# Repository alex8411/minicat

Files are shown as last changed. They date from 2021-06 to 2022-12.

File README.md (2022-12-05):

# minicat
## What's it minicat?
MiniCat is an open source (MIT licence) DIY Robot for Makers and Kids based on Arduino Nano :

- original design (3D parts, hardware, software): [open cat](https://github.com/petoicamp/opencat)
  from: [Rongzhong Li](https://www.linkedin.com/in/rongzhongli/) 

- first training material 
  created by [Lilie Boizumault](https://www.linkedin.com/in/lilie-boizumault/)

- starting from a first prototype below: 

SAM_5404_idle

I developed a plug and play variant of the robot to make it easier to build and understand :

PCB_MiniCat_with_1xServoMG90S_and_2x18650Batteries

MiniCat Robot - Robotics for Makers__MAIN

## Goals

Build a robot with kids and adults that is open source and affordable,
take a look on a comparaison of other kits made by ["le monde"](https://www.lemonde.fr/guides-d-achat/article/2020/06/13/les-meilleurs-kits-robots-pour-les-debutants_6042730_5306571.html)

All the workshops slides are available here under the /Workshop folder

## How pull request

1. Fork the project
2. `$ git clone https://github.com/<your-username>/minicat`
3. `$ cd minicat`
4. `$ git checkout -b branch-name`
5. edit, commit, push file
6. on your browser, in your repo, a button appear (compare and pull request), clic on

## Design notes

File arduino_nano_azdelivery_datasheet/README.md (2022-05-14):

Please find :

- the AzDelivery Arduino Nano clone datasheet : to check all pins available on the board

- the Arduino Nano board official schematics from :
https://www.arduino.cc/en/uploads/Main/Arduino_Nano-Rev3.2-SCH.pdf

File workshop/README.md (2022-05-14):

those are the slides used for MiniCat Robotics/Arduino workshops at Schools, Fablabs/Makerspaces, public events :

- Robotics_for_Makers_MiniCat_Assembly_Guide.pdf : if you want to print and assemble your whole robot !
- Robotics for Makers_Workshop_and_Curriculum.pdf : if you want to get a touch on designing/printing parts, assemble the electronics and program it!

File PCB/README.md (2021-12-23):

MiniCat_2.0_PCB_1_0.fzz is the 2 layers PCB (Printed Circuit Board, top and bottom) for the MiniCat 2.0 robot.

A PCB basically spares you all the manual wires connections that were done in MiniCat 1.0.

This avoids manual connections errors and add robustness to the prototype.
In that way you can concentrate on the different processing, actuators and sensors.

It allows a highly modular / easy to assemble robot.

You can connect all the modules step by step and test them with the related Arduino Software :
- Module 1 : Arduino main Microcontroller board
- Module 2 : Buzzer
- Module 3 : Infrared Receiver
- Module 4 : I2C bus connection between main Arduino Microcontroller board and MPU (Gyroscope)
- Module 5 : MPU (Gyroscope)
- Module 6 : Servo Motors and Driver board (tested together with MiniCat final Software)

MiniCat_2.0_PCB_1x_LAYER_1_0.fzz implements the same connections but this time on 1 top layer only.
This was optimized in order to be able to prototype the PCB on a CNC Mill.

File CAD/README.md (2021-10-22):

Here the .step files which are the 3D parts / Assembly designed in a CAD tool (CAD = Computer Aid Design) e.g. Autodesk Fusion360 or Dassault Systèmes Solidworks.

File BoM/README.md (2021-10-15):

This is the Bill Of Material of all Electronics and Mechanical components needed to build MiniCat.

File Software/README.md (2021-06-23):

Here some hints about the Libraries you will need in order to compile the code for MiniCat :
- Libraries are code files needed to allow special hardware you add to your design to be controlled / managed by the Arduino Nano code
- To add Libraries you need to download their related code and #include them in your main .ino MiniCat Code
- To do so, open your Arduino and go to : Sketch/Include Library/Manage Libraries... then search for the Library you want to download, see details below 
- Libraries you then installed are stored per default under: Documents\Arduino\libraries\I2Cdev

Here the Libraries you need for MiniCat :

Official Arduino Libraries (already installed w/ the IDE) :

- "Wire" / #include <Wire.h> : 
This official Arduino library comes already with your IDE installation and allows you to communicate with I2C devices 
- the MiniCat ArduinoNano board 1 (Master) has the ServoDriver board (Slave) and the Intertial Measurement Unit IMU board (Slave) as I2C devices
  Note that for the IMU board it is not including directly the official I2C Wire lib but is is included through I2Cdev.h (for supporting other boards too), see below
- the MiniCat ArduinoNano board 2 (Master) has the OLED boards (Slave) as I2C devices

- "EEPROM", #include <EEPROM.h>, Library to access the external EEPROM Memory present on the Arduino Nano board. 
This EEPROM memory is non volatile (means robust to MCU Hard Reset) and allows to store the Servomotors calibration data (you need to calibrate only once !)

Additional Libraries specific to MiniCat needs :

- "IRremote 2.2.3" / "#include <IRremote.h>": 
Need to be installed to control MiniCat with an Infrared remote control through the Infrared receiver on Arduino Nano

- "Adafruit PWM Servo Driver Library 2.4.0" ,#include <Adafruit_PWMServoDriver.h> :  
Need to be installed for communicating over I2C to the Servo Driver Board 
(board needed to extend the Arduino Nano as it has only 6 x PWM outputs and we have 8 servo motors to control (2x per MiniCat leg))

- "MPU6050", #include #MPU6050_6Axis_MotionApps20.h" :
Need to be installed to operate the MPU (gyro+accelerometer) via I2C, this MPU Library was written by Jeff Rowberg as well as the custom I2C communication lib below
- "I2Cdev", #include "I2Cdev.h"

- "U8g2 2.28.10", #include <U8g2lib.h> : 
Need to be installed for communicating over I2C to the OLED displays 
Remark: both displays used here have the same I2C address : 0x3C, can be modified to 0x3D by unsoldering a resistor, see in your OLED display spec

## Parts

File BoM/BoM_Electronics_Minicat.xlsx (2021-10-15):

File name | Link | Quantity | Remark | Best Price per unit with small amount! | Total price
MCU board "Adafruit Metro Mini" or other (= Arduino nano SW compatible) | https://www.amazon.de/gp/product/B078SBBST6/ref=ppx_yo_dt_b_asin_title_o04_s00?ie=UTF8&psc=1 | 2 | "Adafruit Metro Mini" or other (= Arduino nano SW compatible) One Arduino for the Servo Control and one for the Eyes Displays | 3.33 | 6.66
IR Sensor + Remote Control | https://www.amazon.de/gp/product/B07DJ58XGC/ref=ppx_yo_dt_b_asin_title_o00_s00?ie=UTF8&psc=1 | 1 |  | 3.99 | 3.99
Buzzer | https://www.amazon.de/gp/product/B073RH8TQK/ref=ppx_yo_dt_b_search_asin_title?ie=UTF8&psc=1 | 1 |  | 1.665 | 1.665
Driver PWM based on PCA9685 chip (Adafruit or other) | https://www.amazon.de/gp/product/B07V72VBJ4/ref=ppx_yo_dt_b_asin_title_o05_s02?ie=UTF8&psc=1 | 1 |  | 6.99 | 6.99
MPU6050 IMU | https://www.amazon.de/gp/product/B07P5YXBXV/ref=ppx_yo_dt_b_asin_title_o05_s02?ie=UTF8&psc=1 | 1 |  | 2.663333333 | 2.663333333
batteries support box | https://www.amazon.fr/gp/product/B08CY5DH1Y/ref=ppx_od_dt_b_asin_title_s00?ie=UTF8&psc=1 | 1 | order the right model : 2P with cover (= for 2 batteries and Box cover) | 1.998 | 1.998
 |  |  |  |  | 0
lithium batteries 3,7V | https://www.amazon.de/gp/product/B07YKVWPRT/ref=ppx_yo_dt_b_asin_title_o03_s00?ie=UTF8&psc=1 | 2 | Remark : as ref. Other Batteries types possible, as long as >5V total and enough current for the 8 servos (peak 0,8 A per servo) e.g. 14500 batteries / 3,7V 800 mAh | 11.995 | 23.99
 |  |  |  |  | 0
batteries charger | https://www.amazon.fr/gp/product/B0747K3YHM/ref=ox_sc_act_title_1?smid=A1X6FK5RDHNB96&psc=1 | 1 | just as a reference example, any Lithium battery charger for 18650 batteries is ok. | 10.67 | 10.67
MG92B servomotors | https://www.banggood.com/6PCS-MG92B-Robot-13_8g-3_5KG-Torque-Metal-Gear-Digital-Servo-For-RC-Airplane-p-1428931.html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 | 8 | ordered 6 on banggood and 10 on AliExpress, Banggood was the cheapest but and faster (<2weeks shipment from China) | 6.573333333 | 52.58666667
 | https://www.aliexpress.com/item/32255083223.html |  |  |  | 0
Display Eyes | https://www.amazon.de/gp/product/B074N9VLZX/ref=ppx_yo_dt_b_asin_title_o04_s00?ie=UTF8&psc=1 | 2 |  | 3.33 | 6.66
USB to micro USB adapter | https://www.amazon.de/PremiumCord-Kabel-USB-B-Mini-5pins/dp/B07NSMMVB2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 | 1 |  | 1.83 | 1.83
springs | https://www.amazon.fr/gp/product/B00GN3BJT4/ref=ox_sc_act_title_1?smid=A2EQEG7VIXTZGJ&psc=1 | 8 | 6,5 x 10mm, not available as single parts, need to buy full set of springs | 11.32 | 11.32
 |  |  |  |  | 0
screw M2 - 6mm, non flat | https://www.amazon.fr/gp/product/B076ZV44GN/ref=ox_sc_act_title_2?smid=A3MWTOW3Y5FBF1&psc=1 | 13 | not available as single parts, need to buy full set of screws of different sizes 2x for MPU6050 / Board support 4x for Servodriver PWM / Board support 2x for Adafruit Metro Mini / Body 1x for IR Sensor / Body 4x batteries box / Box support | 16.59 | 16.59
screw M2 - 8mm, non flat | https://www.amazon.fr/gp/product/B076ZV44GN/ref=ox_sc_act_title_2?smid=A3MWTOW3Y5FBF1&psc=1 | 28 | see line 32: not available as single parts, need to buy full set of screws of different sizes 4x for batteries box / Boards support 4x for feet / legs 8x for servomotors support / legs 8x for servomotors support / body 4x for board support / body | 0 | 0
screw M2 - 8mm + nut, flat | https://www.amazon.de/gp/product/B073SS7D8J/ref=ppx_yo_dt_b_search_asin_image?ie=UTF8&psc=1 | 1 |  | 28.99 | 28.99
wires | https://www.amazon.de/dp/B07KFQ6483 |  |  | 4.66 | 0
ice cream stick | 3D PRINTED | 8 | NOT NEEDED / 3D PRINTED for MiniCat Body, (Body A x4 - Body B x2 - legs x4) | 0 | 0
screw for servomotors support | provided with servos, 2 screws per Servo | 16 | Vis servo _ grande | 0 | 0
screw for servomotors arm | provided with servos, 1 screw per Servo | 8 | Vis servo _ petite | 0 | 0
Software | https://github.com/alex8411/minicat | 1 | Open Source, see link | 0 | 0
3D Printed parts |  |  | 3D printer cost and PLA Plastic filament (30EUR 1kg) cost not included. 180EUR Ender 3 Pro 3D Printer is enough for printing all parts of Minicat | 0 | 0
TOTAL BoM Cost (without 3D printed parts and screws / springs (only sold as kits)) |  |  |  |  | 176.603

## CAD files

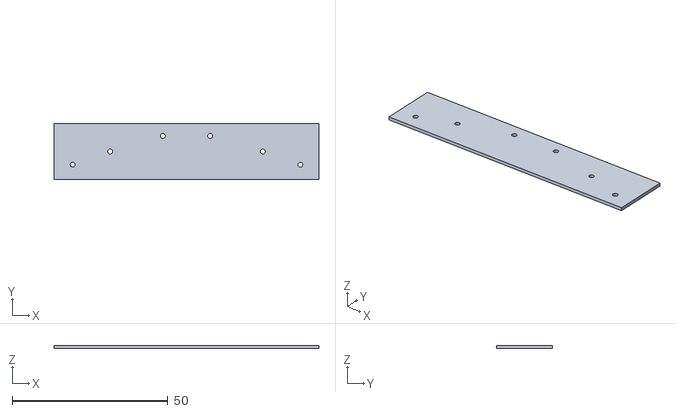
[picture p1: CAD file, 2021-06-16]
3D_printing/STL/10__Body_B_Back.stl
85.0 x 18.0 x 1.00

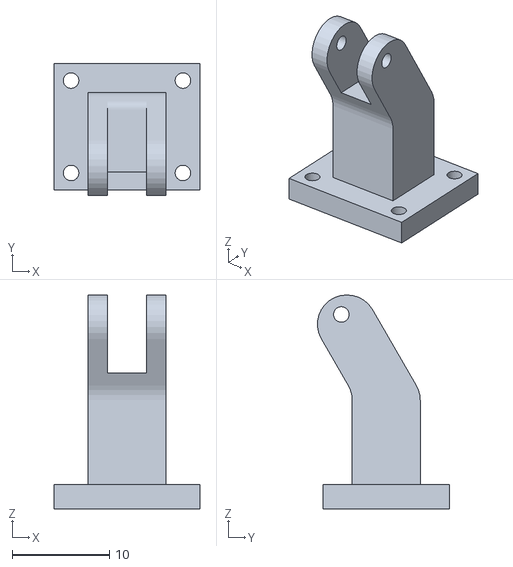
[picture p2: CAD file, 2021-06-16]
3D_printing/STL/minicat_eyes_STL/6__Pied_2_yeux.stl
15.0 x 13.6 x 22.0

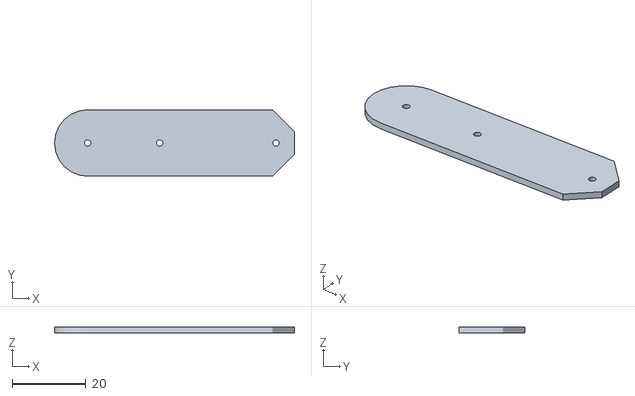
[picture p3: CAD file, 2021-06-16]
3D_printing/STL/9__1_miniShank_Batch3.stl
65.0 x 18.0 x 1.50

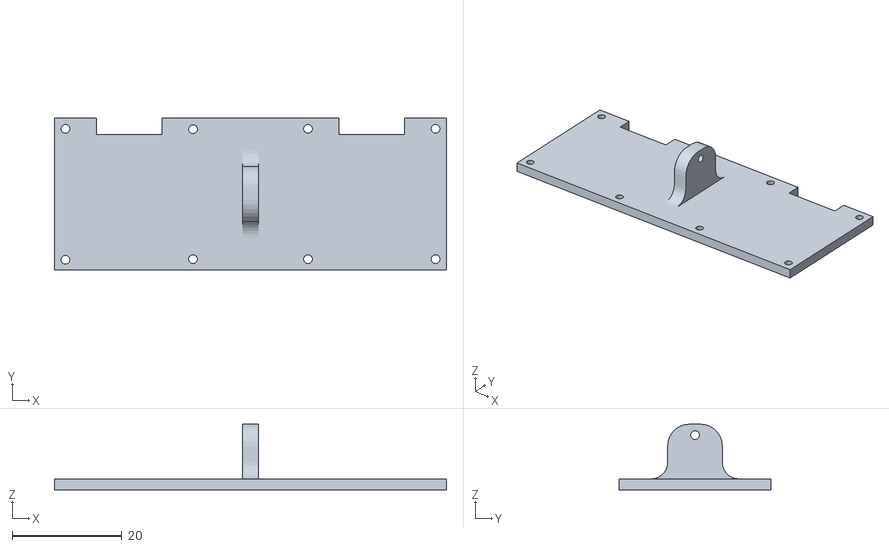
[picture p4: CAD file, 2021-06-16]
3D_printing/STL/minicat_eyes_STL/7__Support_2_yeux.stl
71.6 x 27.8 x 12.0

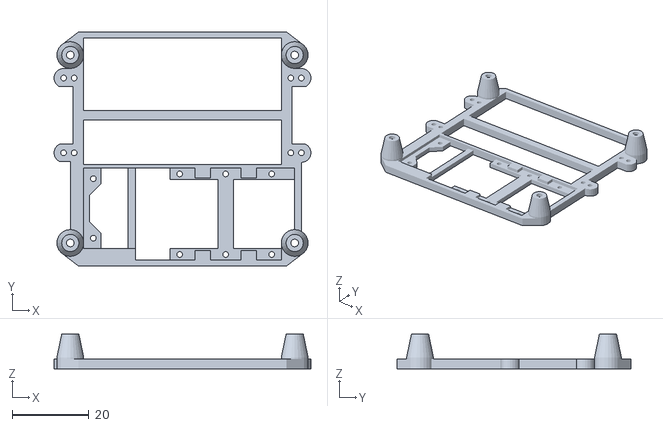
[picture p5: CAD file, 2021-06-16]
3D_printing/STL/5__miniCircuit.stl
67.0 x 61.0 x 9.00

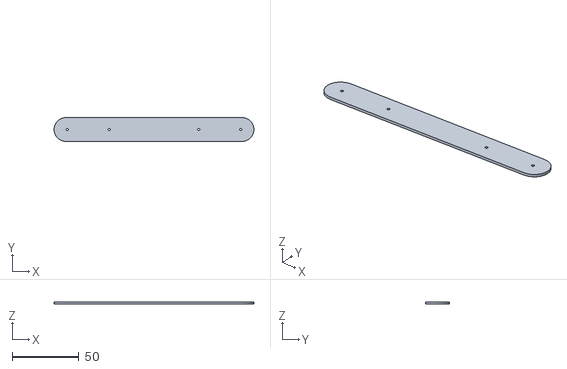
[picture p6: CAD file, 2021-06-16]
3D_printing/STL/8__1_miniBodyA_Batch3.stl
150.0 x 18.0 x 1.50

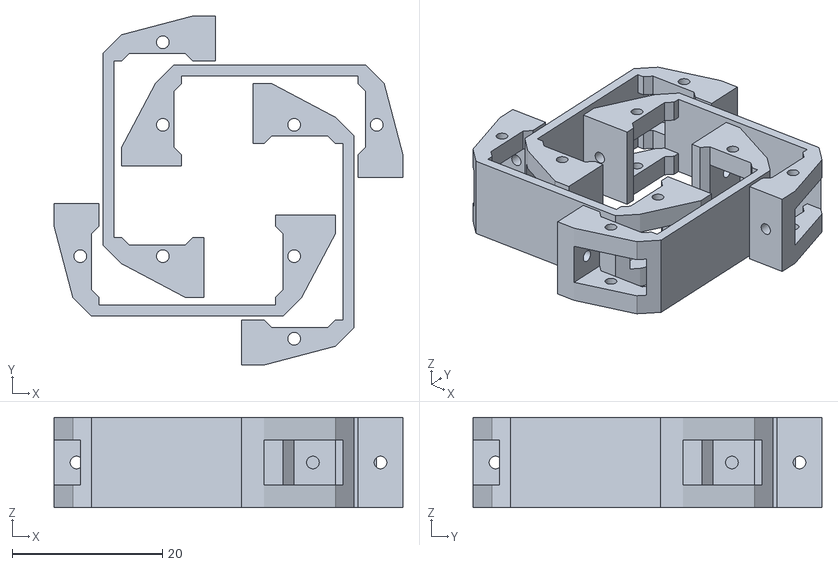
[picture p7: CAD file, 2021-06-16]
3D_printing/STL/2__all_miniServoHolder_Batch1.stl
46.5 x 46.5 x 12.0

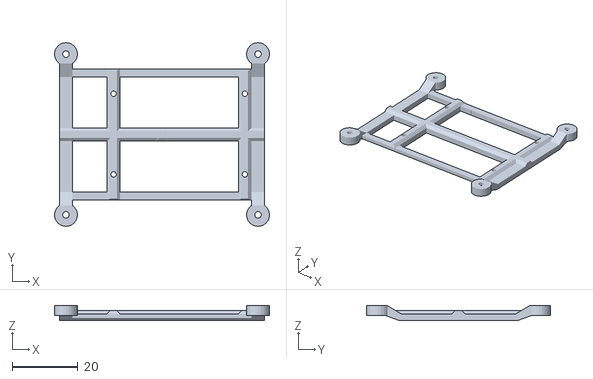
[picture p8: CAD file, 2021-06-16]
3D_printing/STL/4__Battery_holder_FINAL_STL.stl
65.5 x 56.0 x 4.50

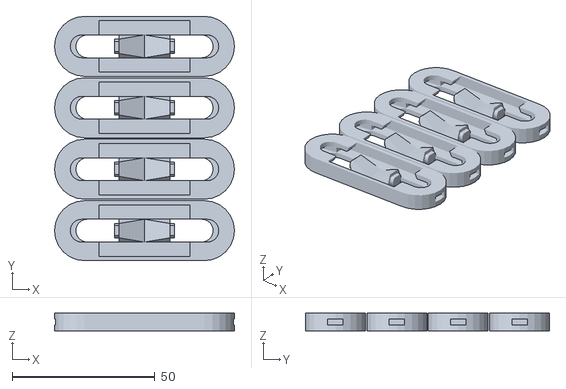
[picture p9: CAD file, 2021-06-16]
3D_printing/STL/1__all_miniThigh.stl
63.0 x 85.5 x 6.20

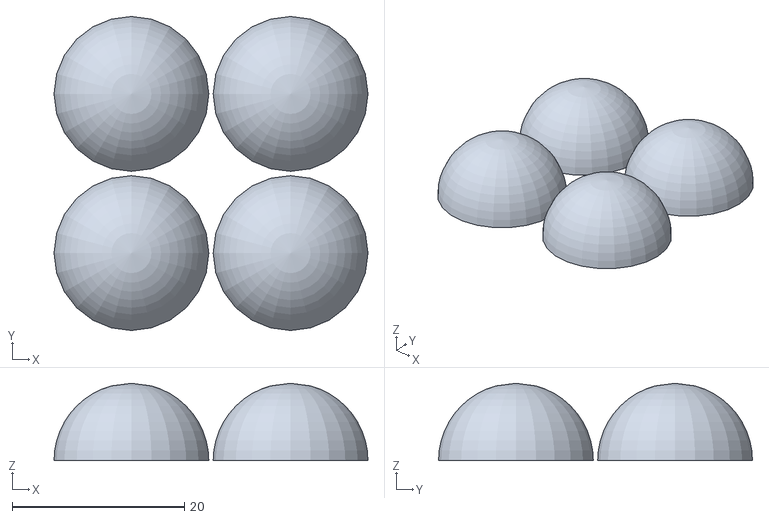
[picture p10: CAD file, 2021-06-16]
3D_printing/STL/3__all_miniToe_rubber.stl
36.5 x 36.5 x 9.00

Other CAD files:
3D_printing/STL/11__Body_B_Front.stl
CAD/MiniCat_full_assembly v32.f3d

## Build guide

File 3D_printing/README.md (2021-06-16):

Here the files you need to produce a complete MiniCat kit :

- the original .STL files : 
  -  those are the meshed files that you can import in any Slicer software to print them (Cura, Prusa, Creality etc..) 

- the 3D Printer (Anycubic Chiron) project file :
  -  the project file will use the .gcode machine code files that will be used directly by the printer
  -  the Anycubic Chiron has the benefit of a very wide Heatbed (400 x 400 x 450mm) that allow you to produce the full MiniCat kit overnight (around 11hours)

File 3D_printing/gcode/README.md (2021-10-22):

Here as an example I provide gcode for the print of all parts of MiniCat. 
The gcode format is the machine code that the 3D printer uses to move the stepper motors and control the extruder.

WARNING !

This is just as an example and I do not recommend to print all parts at once 
as different parts have different heights and the more parts you have on your printing plate, the highest the risk of failure !

My recommendation is to generate gcode and print parts as batches as already grouped in the STL folder.

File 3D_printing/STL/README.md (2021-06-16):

Those are the .STL (3D models of MiniCat parts as mesh files)

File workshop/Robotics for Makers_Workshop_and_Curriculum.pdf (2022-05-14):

E A S Y R O B OT I C S
F O R M AT I O N F O R
M A K E R S

# MINICAT WORKSHOP

Affordable robotics for makers

- Build your full robot from scratch !
- Workshop at Schools / MakerFabs

# AGENDA

## − Workshop Introduction

## − 3D Parts models & Printing

## − Hardware Modules & Test

## − Final Software Integration

# AGENDA

## − Workshop Introduction

## − 3D Parts models & Printing

## − Hardware Modules & Test

## − Final Software Integration

# Workshop Overview

## MiniCat Robot modules

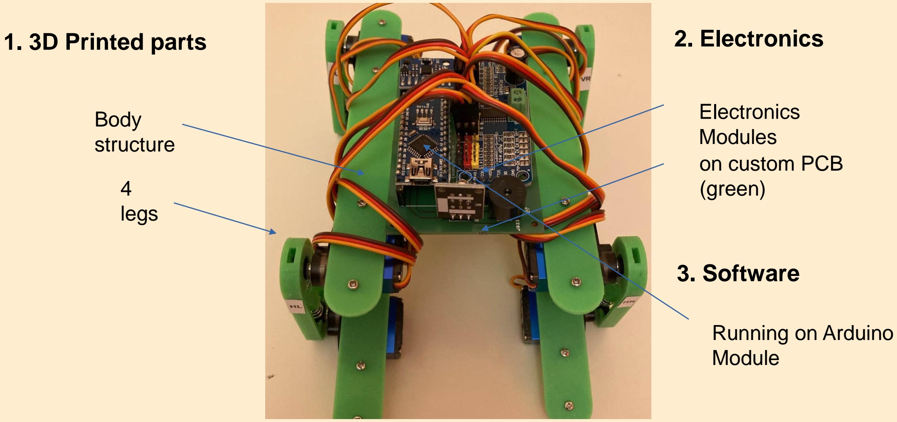
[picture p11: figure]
1. 3D Printed parts; 2. Electronics; on custom PCB (green); Electronics Modules; 3. Software; Running on Arduino Module

Body
structure

4
legs

## Workshop Overview

Maker tools installation check (https://roboticsformakers.com/index.php/maker-software-tools/) w/ participants

- Modelling
- Fusion360 tool
- .stp files
- Slicing/Printing
- Cura tool
- .STL files
1. Tools for 3D Print | 2. Tools for Electronics
- no in scope

### 3. Software

- Development Environment
- Arduino IDE tool

## Workshop Overview

## Toolset installation (to do before workshop)

- Open : https://roboticsformakers.com/index.php/maker-software-tools/
- Follow the instructions to install all the Maker tools

# Workshop Overview

## Software download

- Open : https://github.com/alex8411/minicat
- Click on “Code” then “Download ZIP”:
- Store the ZIP in your preferred Folder & extract it to get “minicat-main”

ToDo :
- Explore the folder especially :
- “3D_printing”
- 3D parts for modelling & 3D print
- “Software” for MiniCat Modules
- GIT .ino files
- Remark: Libraries (https://roboticsformakers.com/index.php/maker-software-tools/) to install separately

# AGENDA

## − Workshop Introduction

## − 3D Parts models & Printing

## − Hardware Modules & Test

## − Final Software Integration

# 3D parts models & printing

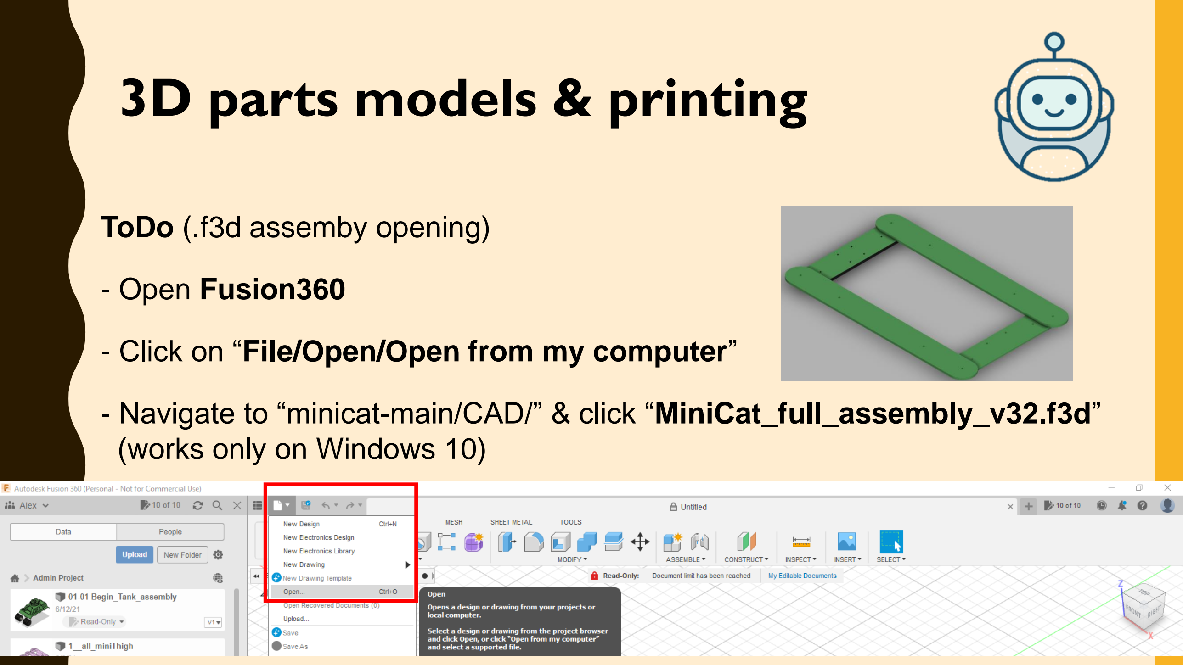
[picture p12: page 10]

ToDo (.f3d assemby opening)

- Open Fusion360
- Click on “File/Open/Open from my computer”
- Navigate to “minicat-main/CAD/” & click “MiniCat_full_assembly_v32.f3d” (works only on Windows 10)

# 3D parts models & printing

ToDo (Sketch opening & modifying)

- Navigate to:
- “minicat_body_central_front_COMPONENT”
- “Sketches”
- “minicat_body_central_front_SKETCH”
- Right click on: “minicat_body_central_front_SKETCH”
- “Edit Sketch”
- Try to modify it

# 3D parts models & printing

- ToDo Editing the Sketch front part : rectangle and hole dimensions:
- click on “Finish Sketch” and observe the changes

# 3D parts models & printing

- Changing the Extrusion dimension :

# 3D parts models & printing

- - measuring with “Inspect” a dimension :

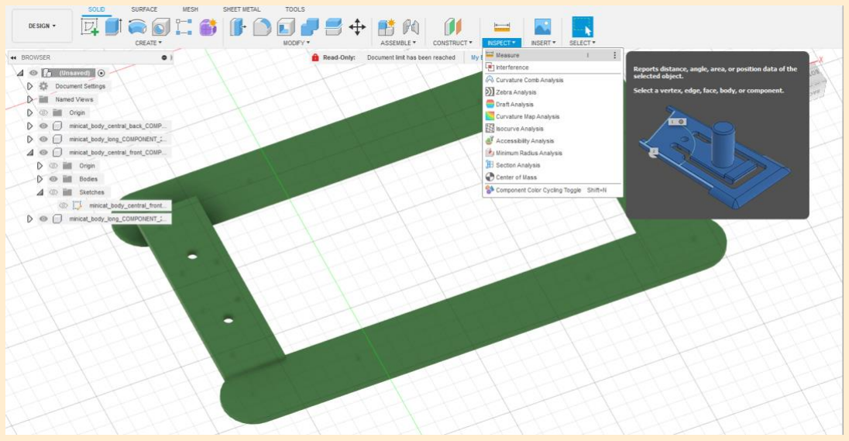
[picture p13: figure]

- - and gravity center :

# 3D parts models & printing

ToDo (.STL file generation)

- Navigate to: “minicat_body_central_front_COMPONENT”
- “Bodies”
- “minicat_body_central_front_BODY”
- “Activate” the “minicat_body_central_front_COMPONENT”

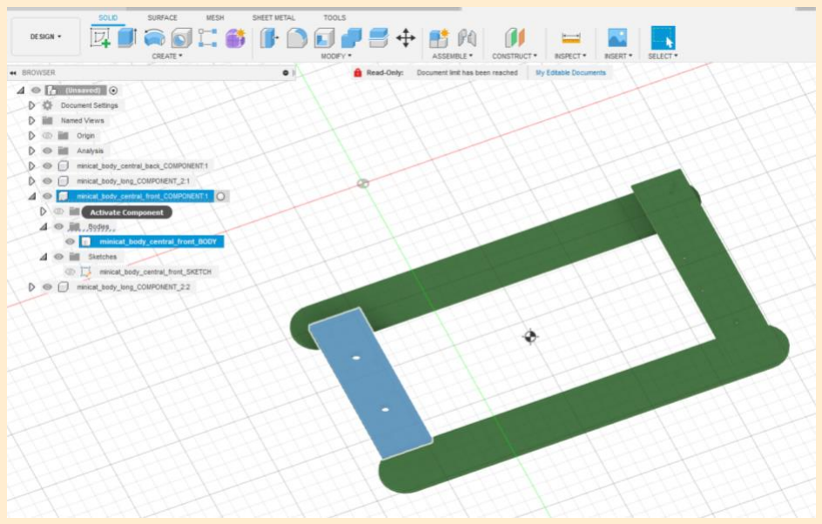
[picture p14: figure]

# 3D parts models & printing

ToDo (.STL file generation)

- Right click on “minicat_body_central_front_BODY”
- “Save as Mesh” (=“als Netz speichern”)
/ and select Format “STL (Binary)” / “Save”

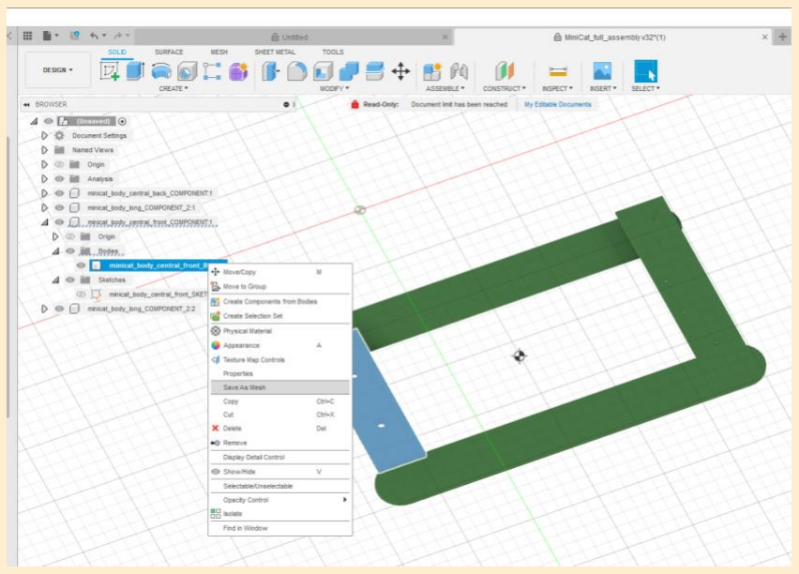
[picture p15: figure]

# 3D parts models & printing

ToDo (.STL file generation)

- Open CURA and Add a Non Networked Printer “Creality Ender3 Pro”
- “File/Open file(s)” the .STL file you just generated !
- “Slice” it !
- Check the “Preview” / click on “Play” button
- “Save to Disk” to save it as a 3D Printer Machine code (.gcode)

# 3D parts models & printing

## .STL file, generate your own

ToDo (Opening Toes .STL, Slicing & Simulation)

- For the Workshop we will not use the previously
generated Body STL file but use an existing .STL : “minicat-main/3D_printing/STL/3__all_miniToe_rubber.stl”
- Background :
Printer is now optimized for TPU (“gummi”) print,
not PLA rigid plastic
- Open CURA
- Open “minicat-main/3D_printing/STL/3__all_miniToe_rubber.stl”
- “Slice“ and write the time

# 3D parts models & printing

## .STL file, generate your own

ToDo (3D printer config for TPU)

- Open Cura
- click on “Preferences/Configure Cura/Profiles
- ”Import” the content of “CHEP4.11_TPU” profile
from “minicat-main/3D_printing/printing_profiles/ender3pro/tpu”
- ”Activate” the profile (work on on Mac, Windows10)
- Open your previously generated .STL file
- Slice it and check if the simulated printing time is different with the TPU profile vs “Default/Standard Quality” profile
- “Save to Disk” (.gcode machine code)

# 3D parts models & printing

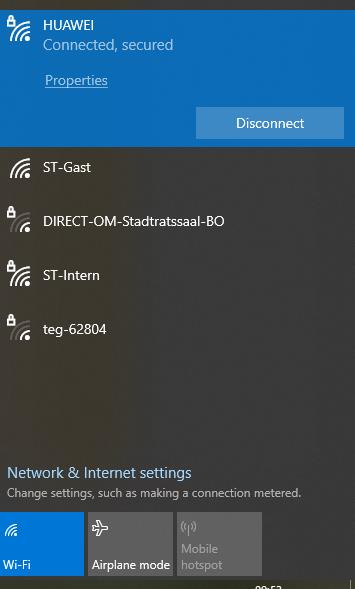
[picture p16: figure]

ToDo (Printing !)

### 3 ways to print a .gcode file :

1- SD Card:
- save generated .gcode and plugin in printer

2- Octoprint Server on Raspi:
- WLAN :
connect to HUAWEI WLAN / Password: 2Groesser?
- Server :
- open http://octopi.local/login in your browser
- login: roboticsformakers / Password: 2Groesser?

3- Octoprint Plugin for CURA: -> Focus today
- connect to HUAWEI WLAN / Password: 2Groesser?
- open CURA and install Octoprint Plugin
- start the “Preparation” and Print

# 3D printing

I loaded the TPU (flexible filament profile) in CURA and generated the .gcode for you :

# 3D parts models & printing

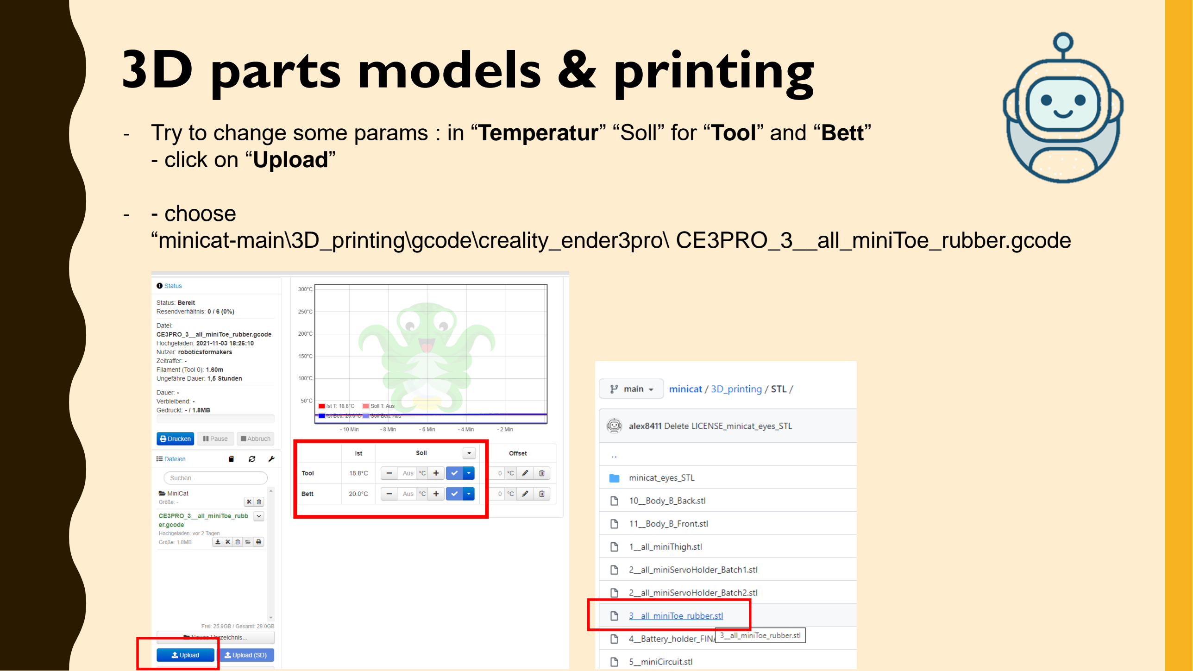
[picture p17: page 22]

- Try to change some params : in “Temperatur” “Soll” for “Tool” and “Bett”
- click on “Upload”
- - choose
“minicat-main\3D_printing\gcode\creality_ender3pro\ CE3PRO_3__all_miniToe_rubber.gcode

# 3D parts models & printing

3D print w/ Octoprint :
- Preheat the Tool (Extruder) at 225°C
- Preheat the Bed at 60°C

# 3D parts models & printing

- IMPORTANT: Ask the teacher first !
- only one participant can start the printing after another !

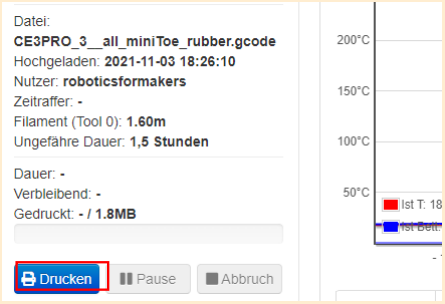
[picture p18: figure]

End of
the 2h

After the
2 hours
break :

# AGENDA

## − Workshop Introduction

## − 3D Parts models & Printing

## − Hardware Modules & Test

## − Final Software Integration

# Hardware Modules & Test

Overview | Module 1: Arduino board
- “Brain” of the robot, runs Software

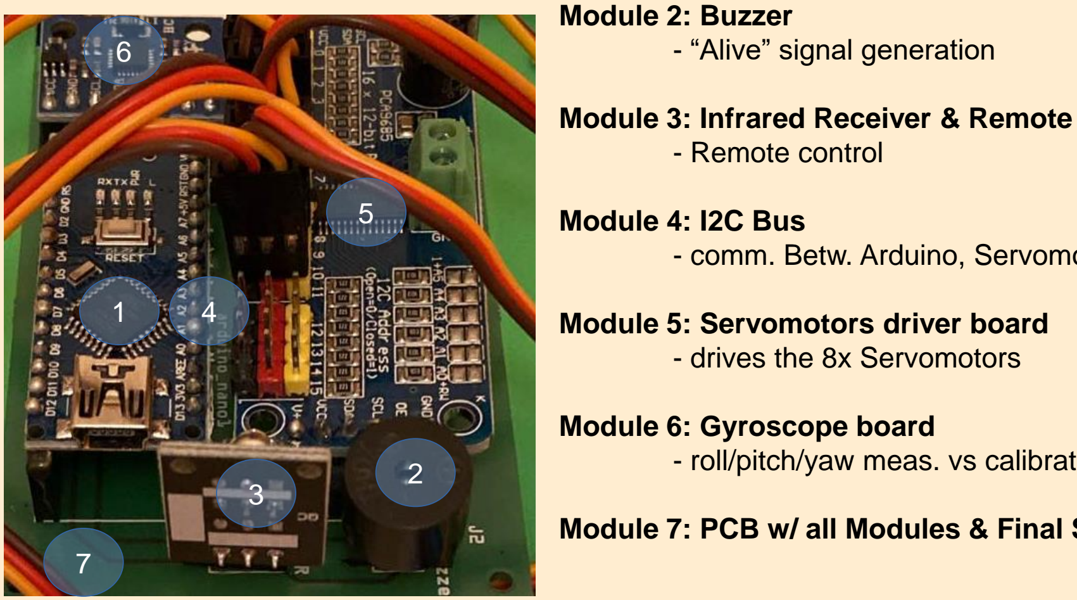
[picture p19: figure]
Module 2: Buzzer - “Alive” signal generation; Module 3: Infrared Receiver & Remote - Remote control; Module 4: I2C Bus; Module 5: Servomotors driver board - drives the 8x Servomotors; Module 6: Gyroscope board

- comm. Betw. Arduino, Servomotors & Gyro boards
- roll/pitch/yaw meas. vs calibrated 0 for robot balance

Module 7: PCB w/ all Modules & Final Software

- comm. between Arduino, Servomotors & Gyro
- roll/pitch/yaw meas. vs calibrated 0 for robot

Module 7: PCB w/ all Modules & Final Software

# Hardware Modules & Test

## Module 1: Arduino Board, blink Led

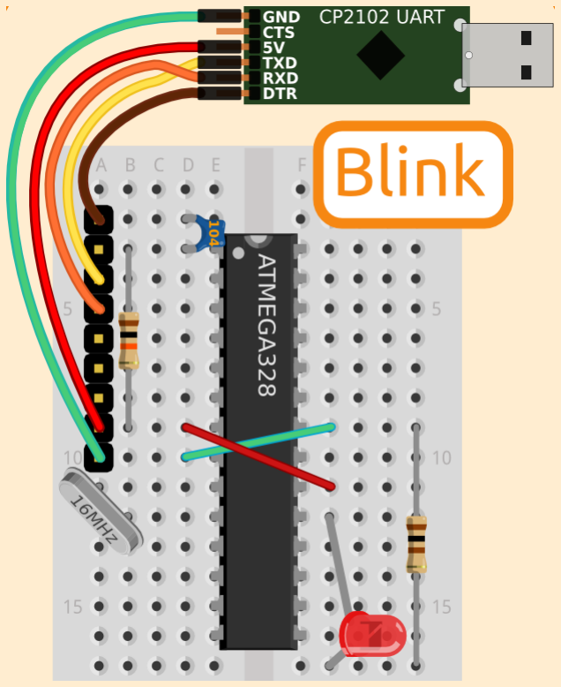
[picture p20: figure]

Official Arduino docu: Link (https://www.arduino.cc/en/Tutorial/BuiltInExamples/BlinkWithoutDelay)

# Hardware Modules & Test

## Module 1: Arduino Board

Module 1: Arduino board & blink Led
- “Brain” of the robot, runs the Software

ToDo:
- Plugin the provided USB cable to your Laptop
- Start the Arduino IDE

Your Laptop
USB

# Hardware Modules & Test

## Module 1: Arduino Board

ToDo: - Connect Arduino Nano Board w/ PC over USB
- In the IDE, choose the Serial Port “COM*”
- Choose the Board “Arduino Nano”
- Choose the Bootloader “Old Bootloader”

Your Laptop
USB

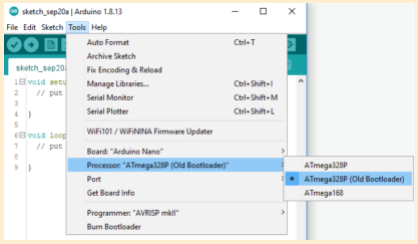
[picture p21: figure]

# Hardware Modules & Test

## Module 1: Arduino Board

ToDo:
- In the IDE, choose the USB / Serial Port you are using :

Your Laptop
USB

# Hardware Modules & Test

## Module 1: Arduino Board

ToDo:
- Click on ”File/Examples/Digital/Blink without delay”

Your Laptop
USB

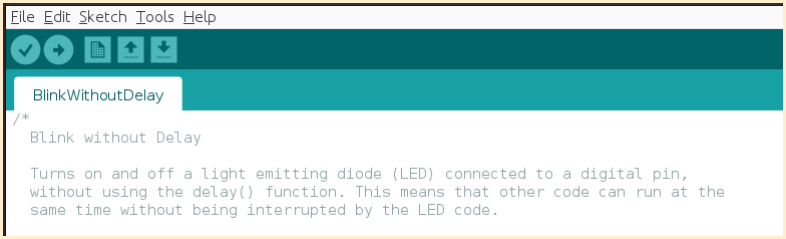
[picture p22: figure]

- For Windows 10, please install USBtoSerial driver „CH340G this is part of MiniCat GIT, (https://github.com/alex8411/minicat/tree/main/Software/usb_to_serial_chip_driver) see Software folder (or „DirectLink“) (http://www.wch.cn/download/CH341SER_EXE.html)
- MacOS and Ubuntu 20.04, no problems, no driver needed

# Hardware Modules & Test

## Module 1: Arduino Board & Led

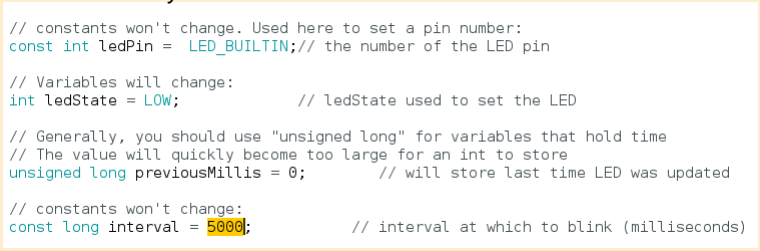
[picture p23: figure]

ToDo (Software):
- Change the blinking interval to 5000 (default 1000=1s)
- Click on “Upload” to start the Software
- Observe the result on the Arduino board

BlinkWithoutDelay.ino

# Hardware Modules & Test

## Module 2: Buzzer

Module 2: Buzzer (https://arduinogetstarted.com/tutorials/arduino-piezo-buzzer)
- inside a buzzer case is a piezo element (ceramic disc)
- once voltage is supplied, the ceramic disk vibrates
- if square signal (PWM) provided sound varies w/ freq.

ToDo:
- Unplug the USB cable from your Laptop
- Plugin the Arduino & Servodriver board on the PCB
- Plugin the USB cable to your Laptop
- open the buzzer test software : double click on “minicat-main/Software/buzzer_test/minicat_buzzer_test.ino”

(+)

## Hardware Modules & Test

## Module 2: Buzzer, modify the code adding:

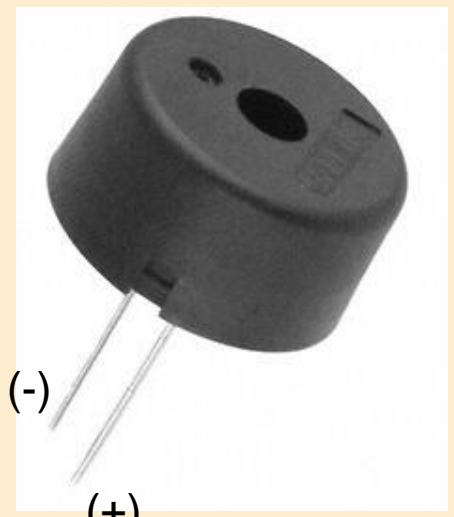
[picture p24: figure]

(+)

int counter = 0;

void loop() {

while (counter < 5)

{

byte melody[] = {8, 13, 10, 13, 8, 0, 5, 8, 3, 5, 8, // definition of the tones list as a "melody"
8, 8, 32, 32, 8, 32, 32, 32, 32, 32, 8 //8,8,16,16,8,16,16,16,16,8
};
playMelody(melody, sizeof(melody) / 2); // we play the melody

}

}

# Hardware Modules & Test

## Module 2: Buzzer

ToDo (Software):
- Change the melody by changing the values / deleting some
- Click on “Upload” to start the Software
- Observe the result on the Arduino board

minicat_buzzer_test.ino

# Hardware Modules & Test

## Module 3: Infrared receiver & remote

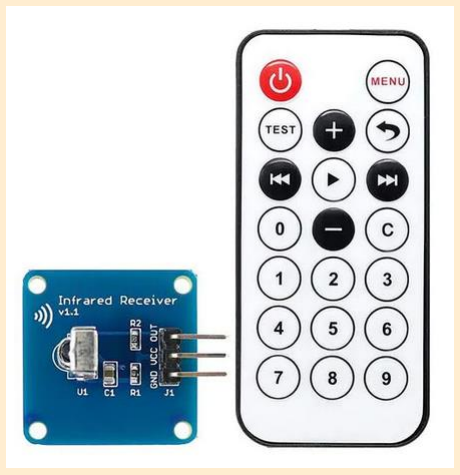
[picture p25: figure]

Module 3: Infrared receiver & remote
- Remote Control
ToDo:
- Unplug the USB cable from your Laptop
- Plugin the Infrared receiver on the PCB
- Plugin the USB cable to your Laptop
- Check if the led is ON when you push the remote
- the Software Library “IRRemote” (https://roboticsformakers.com/index.php/maker-software-tools/) should be installed (Tools/Manage Libraries “IRremote”)
- open the IRRemote test software : double click on
“minicat-main/Software/ minicat_IRremote_test /minicat_IRremote_test.ino”

# Hardware Modules & Test

## Module 3: Infrared receiver & remote

ToDo:
- Open the Arduino Serial Monitor
(Arduino IDE “Tools/Serial Monitor”)
- in serial monitor, set the communication speed to 57600 baud
- Push on the buttons on the Remote control
and verify that they are correct in the Serial Monitor

# Hardware Modules & Test

## Module 3: Infrared receiver & remote

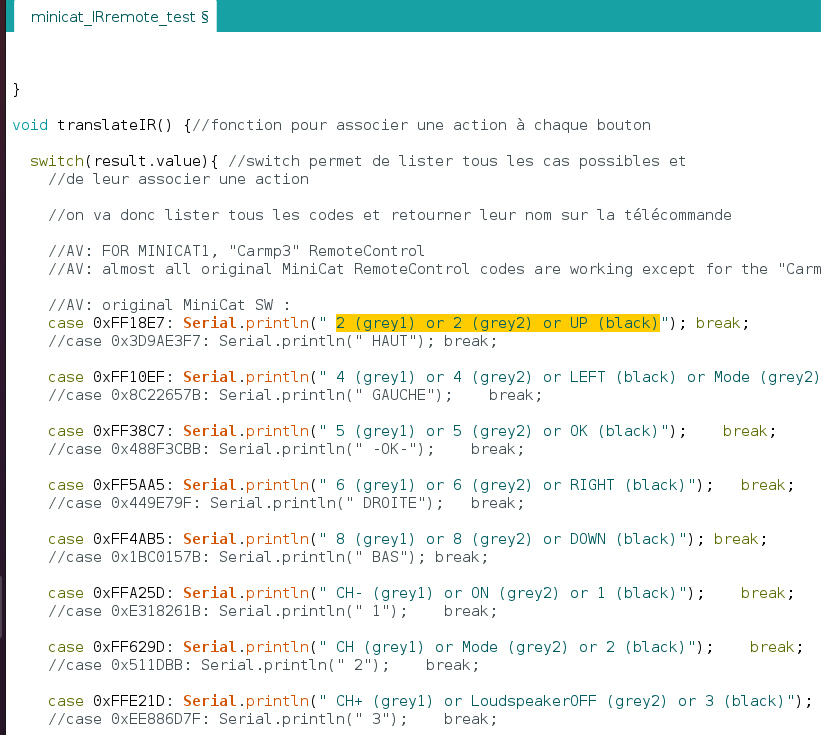
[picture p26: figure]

ToDo (Software):
- change a button description :
- push this button on remote
- verify that it is displayed in the serial monitor

# Hardware Modules & Test

## Module 4: I2C Bus connections

Module 4: I2C Bus connections / devices check
- comm. between Arduino & Servomotors & Gyro boards ToDo:
- Unplug the USB cable from your Laptop
- Plugin the Gyro and Servodrivers boards on PCB
- Plugin the USB cable to your Laptop
- Put the 2 batteries in place and turn ON on holder (MPU6050 need enough power from Servodrivers board)
- I2C library (“Wire”) is installed by default (Arduino IDE)
- open the i2c communication test software: “minicat-main/Software/minicat_i2c_test/minicat_i2c_test.ino”
- 3x I2C devices should appear (serial monitor)

Master
Slave1

Slave2

# Hardware Modules & Test

## Module 4: I2C Bus connections

ToDo:
- Open the Arduino Serial Monitor
(Arduino IDE “Tools/Serial Monitor”)
- Set the communication speed to 57600 baud
- Verify that the 3 I2C Devices are present:
- I2C device found at address 0x40 ! (Servos Driver)
- I2C device found at address 0x68 ! (Gyro)
- I2C device found at address 0x70 ! (Arduino Nano)

Master
Slave1

Slave2

# Hardware Modules & Test

## Module 5: Servomotors driver board

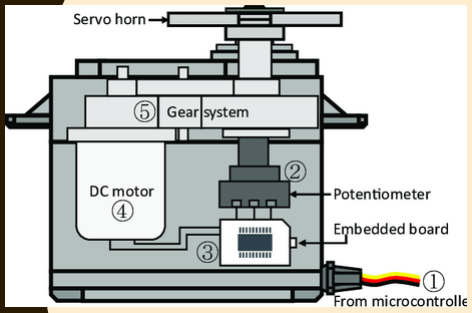
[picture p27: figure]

Module 5: Servomotors driver board
- drives the 8 servos, here we test w/ 1 servomotor
- based on Arduino inputs on I2C
- and Servodriver board 8 x PWM control signals outputs
- we use first 5V supply from Arduino (no batteries)

ToDo:
- Unplug the USB cable from your Laptop
- The 8x Servomotors cables are already plugged

# Hardware Modules & Test

## Module 5: Servomotors driver board

ToDo:
- Plugin the USB cable to your Laptop
- Start the Arduino IDE
- the Software Library
“Adafruit PWM servo driver library” (https://roboticsformakers.com/index.php/maker-software-tools/)
should be installed

(Tools/Manage Libraries “Adafruit PWM Servo Driver Library”)

- open the minicat_one_servo_test software : double click on
“minicat-main/Software/minicat_one_servo_test/minicat_one_servo_test.ino”

# Hardware Modules & Test

## Module 5: Servomotors driver board

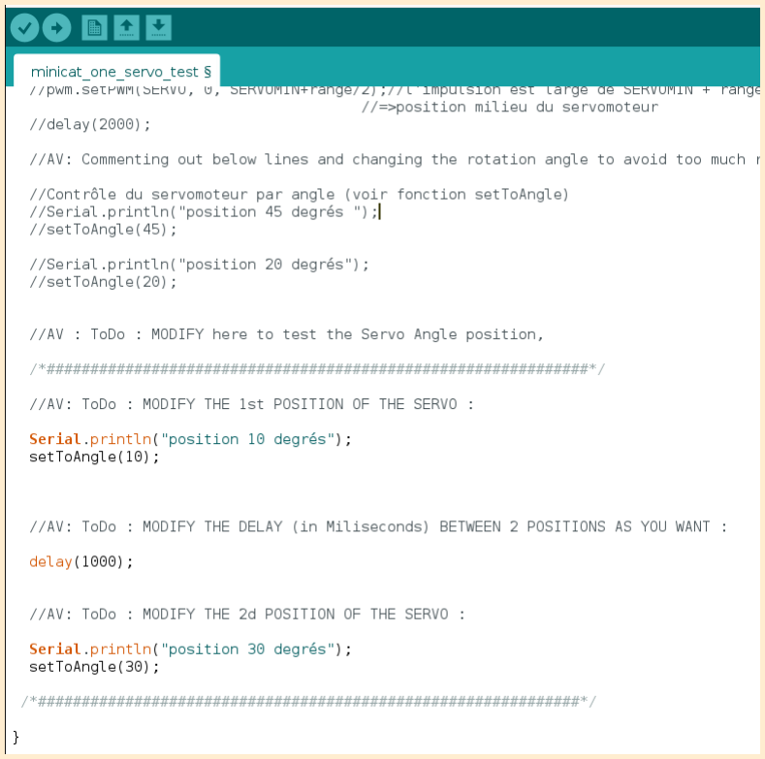
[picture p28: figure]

ToDo (Software):

change servo n.
and delay :

# Hardware Modules & Test

## Module 5: Servomotors driver board

ToDo (Software):
Change the servo number to test all servos one by one :

# Hardware Modules & Test

## Module 5bis: Servomotors driver board

Module 5bis: Servomotors driver board
- we use now the 2x4,2V Lithium batteries supply (your teacher will install them, please ask him)

ToDo:
- Unplug the USB cable from your Laptop
- Ask your teacher to install the 2 x Batteries in the robot
- Put the batteries holder button to “ON” under the robot
- Check if the Servomotor is moving (Front Right Top)

# Hardware Modules & Test

## Module 6: Gyroscope board

Module 6: Gyroscope board
- measuring roll/pitch/yaw
- compared with calibrated “zero”
- compensate the legs height / balance

ToDo:
- Unplug the USB cable from your Laptop
- Plug the Gyro module in the PCB
- Plugin the USB cable to your Laptop
- Start the Arduino IDE’
- Get the Arduino Libraries “I2Cdev and MPU6050” (https://roboticsformakers.com/index.php/maker-software-tools/)
- Start the 1x Gyro test software “minicat_i2c_test.ino”

# Hardware Modules & Test

## Module 6: Gyroscope board

The Gyroscope module need the Libraries “I2Cdev” and “MPU6050” for I2C communication to Gyroscope MPU6050 sensor :
– Open : https://github.com/jrowberg/i2cdevlib
– Click on “Code” and then “Download ZIP”
– the Downloaded .zip is normally stored into your “C:\Users\*UserName*\Downloads” folder
– Unzip the “i2cdevlib-master.zip” in your “C:\Users\*UserName*\Downloads” folder
to get a “i2cdevlib-master” folder

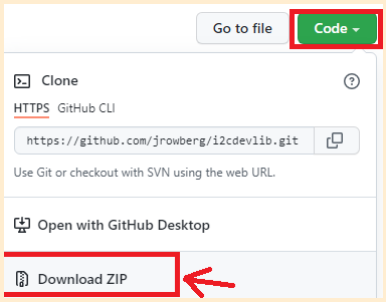
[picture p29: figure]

# Hardware Modules & Test

## Module 6: Gyroscope board

1- Now to add the 2 libs we need,

Click on “Sketch/Include Library/Add .ZIP Library” :

2- Change the “Files of type” to “All Files”
(as we already unzipped) :
3- Navigate to
“C:\Users\*UserName*\Documents\Arduino\libraries\i2cdevlib-master\i2cdevlib-master\Arduino\

# Hardware Modules & Test

## Module 6: Gyroscope board

4- Then Single Click on the “I2Cdev” Folder and then “Open” :

# Hardware Modules & Test

## Module 6: Gyroscope board

5- Repeat the steps above for adding the “MPU6050″ lib :

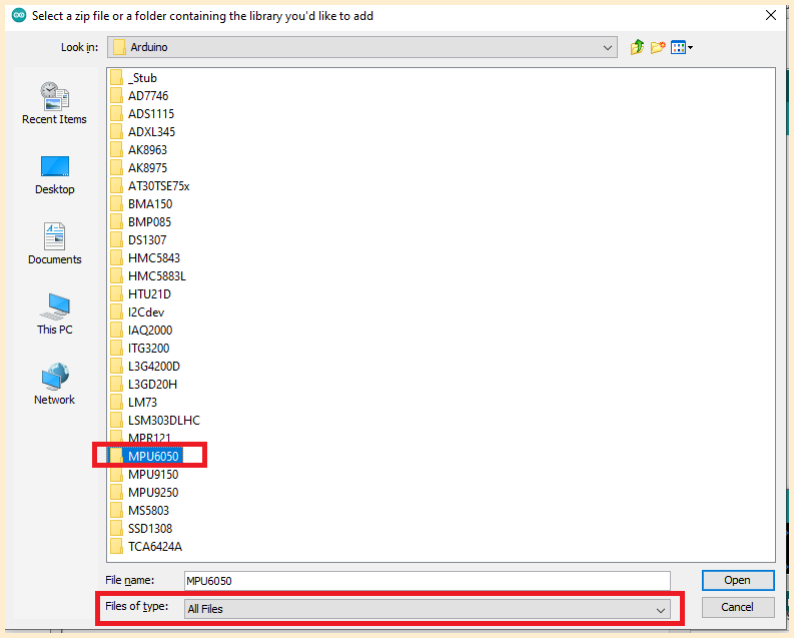
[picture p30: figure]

# Hardware Modules & Test

## Module 6: Gyroscope board

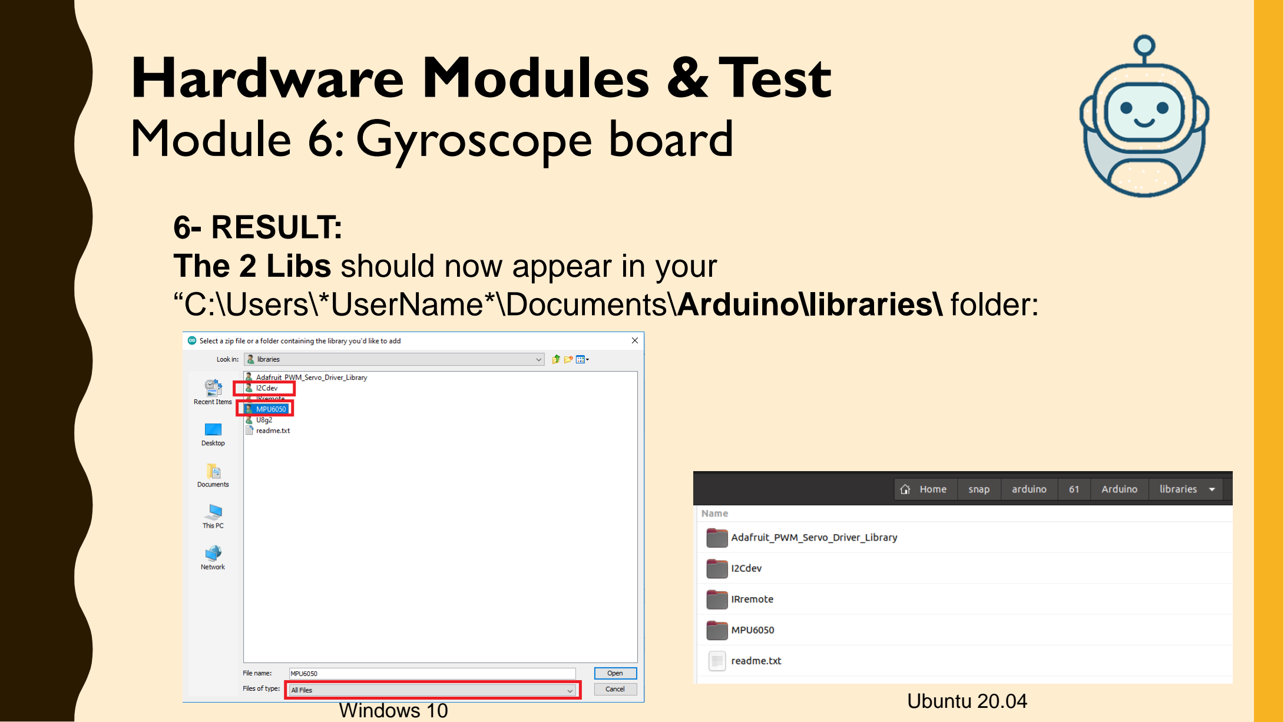
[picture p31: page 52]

6- RESULT:
The 2 Libs should now appear in your “C:\Users\*UserName*\Documents\Arduino\libraries\ folder:
Windows 10 | Ubuntu 20.04

# Hardware Modules & Test

## Module 6: Gyroscope board

ToDo:

- Open the Serial Monitor
- Check the “ypr” = yaw pitch roll values when moving MiniCat : (click on “Autoscroll” to stop)

# Hardware Modules & Test

## Module 7a: All modules + calib

Module 7a: All Modules + calibration
- servos check + gyro calibration
- not in focus of this workshop (time consuming)
- servo need to be placed at their zero (middle) angle
- gyro need to be calibrated to know its zero angles (rpy)

Todo:
- Make sure all modules plugged on the PCB
- Put the battery holder button on “ON” first
- Plugin the USB cable to your Laptop

# Hardware Modules & Test

## Module 7a: All modules + calib

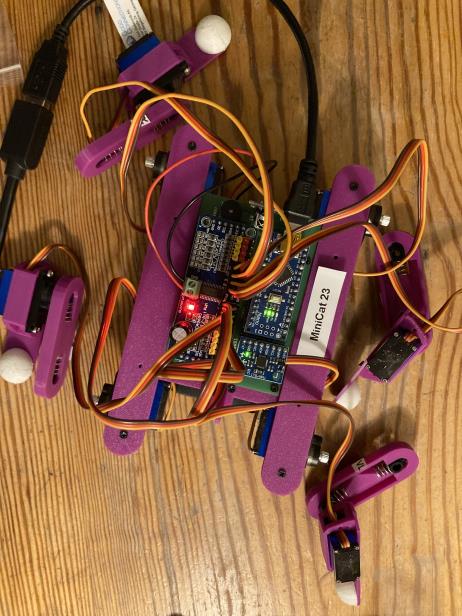
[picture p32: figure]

Todo (Software): calib done, not in focus of workshop

- disconnect all legs of MiniCat, no servo blocked
- make sure MiniCat is on a flat surface
- start the “minicat_servos_and_gyro_calibration.ino”
- Open the Serial Monitor
- “Upload” the Software
- The Gyroscope will measure the MiniCat chassis roll/pitch/yaw angles offsets compared to the MPU6050 chip default zero angles, the offsets will be shown ´’ in the serial monitor

# Hardware Modules & Test

## Module 7a: All modules + calib

Background :

servos calib:
- we need to put all servos at their central zero position before mounting the legs of MiniCat

gyroscope (MPU6050 chip) calib:
- we need to measure the offset of the gyro yaw pitch roll angles compared to the default zero angles in the Gyro board firmware (MiniCat should be put on a flat surface)

Remark :
the gyro angles offset values will be stored in EEPROM
(non volatile memory of Arduino Nano)
so that this Calibration is needed only once on a particular Arduino

# Hardware Modules & Test

## Module 7a: All modules + calib

Todo (Software):

- the gyro and servos calibration process will start
- if everything is fine, you get this output in the serial monitor

# Hardware Modules & Test

## Module 7a: All modules + calib

Todo (Software):
- keep the serial monitor open and
type “c” in the command line then “Enter”
This will place the servos at their central “zero” position
- The Servo angles will be shown w/ zeros in the serial monitor (only 8 to 15 are our 8 servos)
8, | 9, | 10, | 11, | 12, | 13, | 14, | 15
0, | 0, | 0, | 0, | 0, | 0, | 0, | 0,
- Keep the battery holder button on “ON”
- Do not remove the USB cable from your Laptop yet !
- you will only insert the tighs & feet parts in the servos axis see how on next slide, do not turn the servo axis manually ! (as you just set the servos to their zero angle pos.)

# Hardware Modules & Test

## Module 7a: All modules + calib

Todo (Software):

- Now that you have set the servos to their zero angle you can mount them as below
(Hint: do not move the servo axis anymore!
If so, start again
“minicat_servos_and_gyro_calibration.ino”) :

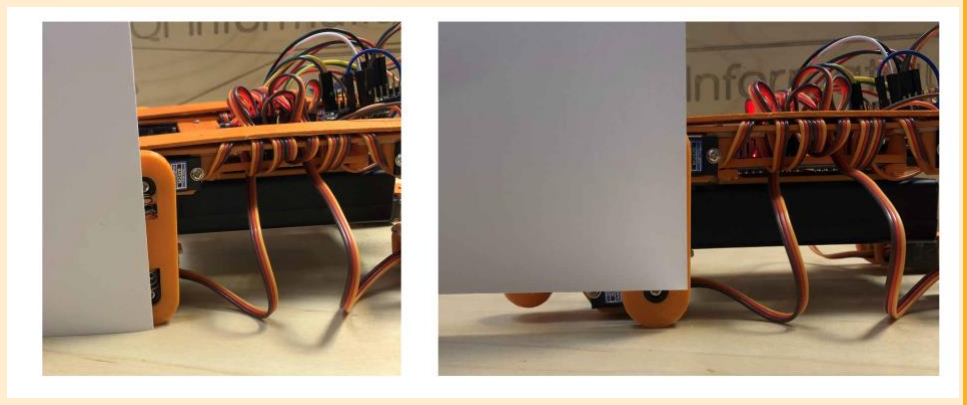
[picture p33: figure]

# Hardware Modules & Test

## Module 7a: All modules + calib

Optional / Todo (Software): Servos angle Fine tuning :
- If you can not achieve 100% the above, you can still fine tune the servo angles by software by running the below in the Serial Monitor:

c “servo link index” “correction angle

For example, if you want to change
the angle of link 12 of +5 deg
you can run : c12 5

Remark : each tooth of the servo axis is 360deg/20teeth so 18deg so the fine tuning makes sense for +/- 9deg, if more needed just remove the servo arm from the servo axis and place it on a next tooth!

FRON
T

Servos indexes reminder

# Hardware Modules & Test

## Module 7a: All modules + calib

Todo (Software):

- put the servo screws in the servo axis to fix the positions :

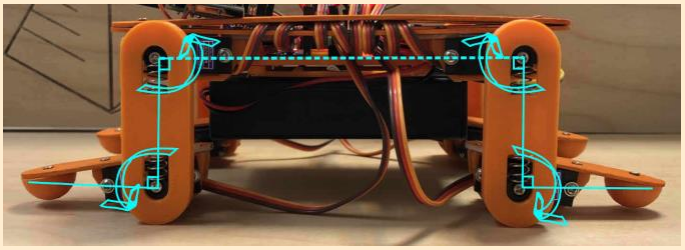
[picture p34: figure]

- Once you have achieved the above, type “s” in the serial monitor (this will save your servos angles calibration in Arduino EEPROM (non volatile))

# Hardware Modules & Test

## Module 7a: All modules + calib

Todo (Software):
- to test your servos calibration, try different positions :
- type “d” in monitor to go in default position (“stop”), expected :
- type “pbalance” to go in “stand” position, expected :

# Hardware Modules & Test

## Module 7b: All modules on PCB

Module 7b: All Modules on PCB and Play !

ToDo:
- Unplug the USB cable from your Laptop
- Make sure all modules plugged on the PCB
- Put the battery holder button on “ON” first
- Plugin the USB cable to your Laptop
- open the minicat_basic software : double click on
“minicat-main/Software/minicat_basic/minicat_basic.ino
- Use the remote control to play !

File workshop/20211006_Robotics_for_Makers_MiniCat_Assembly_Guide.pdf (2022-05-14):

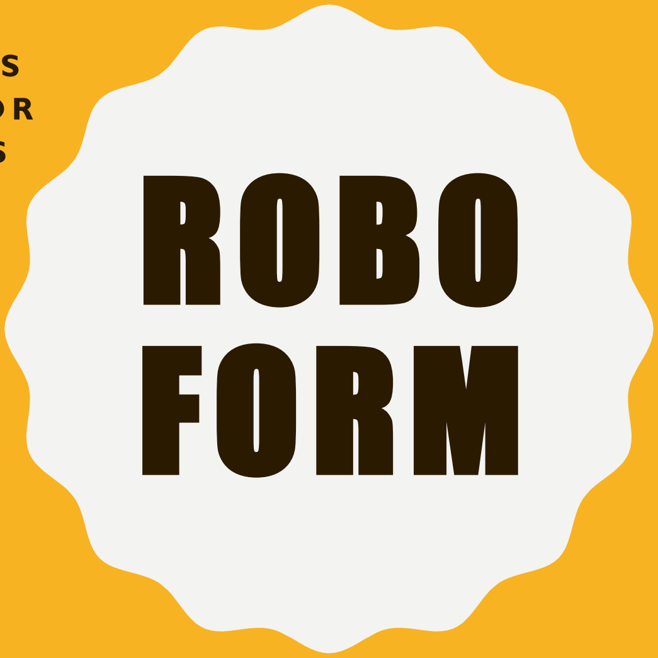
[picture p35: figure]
ROBO FORM

E A S Y R O B OT I C S
F O R M AT I O N F O R
M A K E R S & K I D S

# MINICAT ASSEMBLY OVERVIEW

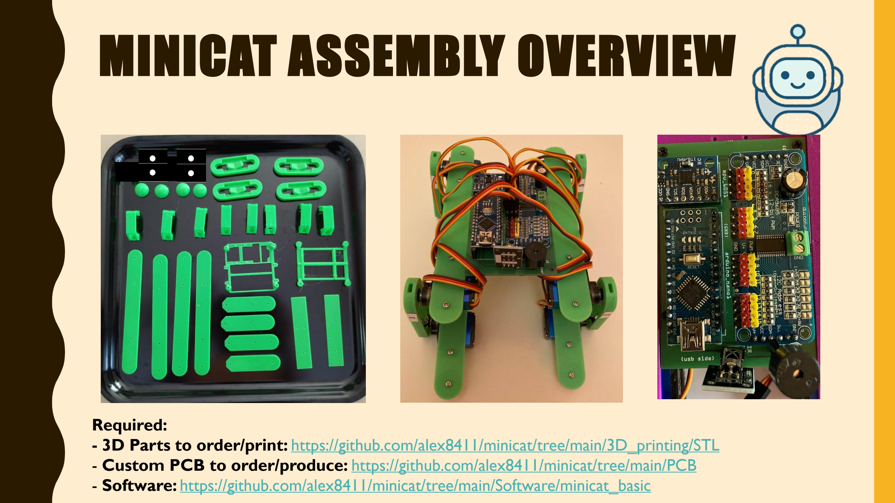
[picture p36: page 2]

Required:
- 3D Parts to order/print: https://github.com/alex8411/minicat/tree/main/3D_printing/STL
- Custom PCB to order/produce: https://github.com/alex8411/minicat/tree/main/PCB
- Software: https://github.com/alex8411/minicat/tree/main/Software/minicat_basic

# MINICAT ASSEMBLY

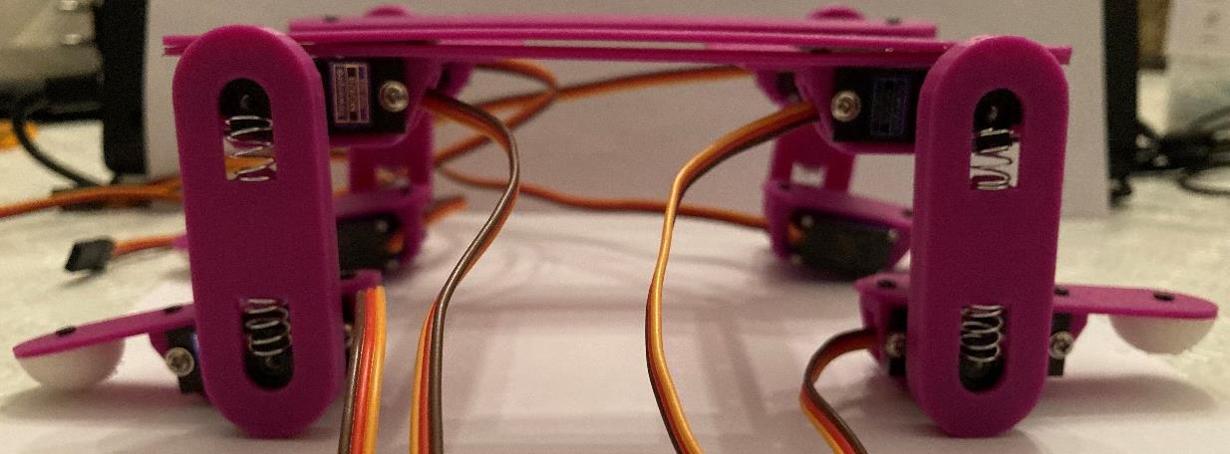
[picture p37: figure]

## Prerequisites : - Flat head and Cross screwdrivers - 3D printed parts: STL (https://github.com/alex8411/minicat/tree/main/3D_printing/STL)

- Screws (M2): 800 Stück M2 schwarzer Kohlenstoffstahl mit Senkkopf und flachem Kreuzkopf, selbstschneidende Schrauben (https://www.amazon.de/gp/product/B07RYLM9N2/ref=ppx_yo_dt_b_search_asin_title?ie=UTF8&psc=1)
- Springs (8,5x10): McDrill Jeu de 246 ressorts de compression (https://www.amazon.fr/gp/product/B00GN3BJT4/ref=ppx_yo_dt_b_asin_title_o04_s00?ie=UTF8&psc=1)

# MINICAT ASSEMBLY

# STEP1.1: FEET

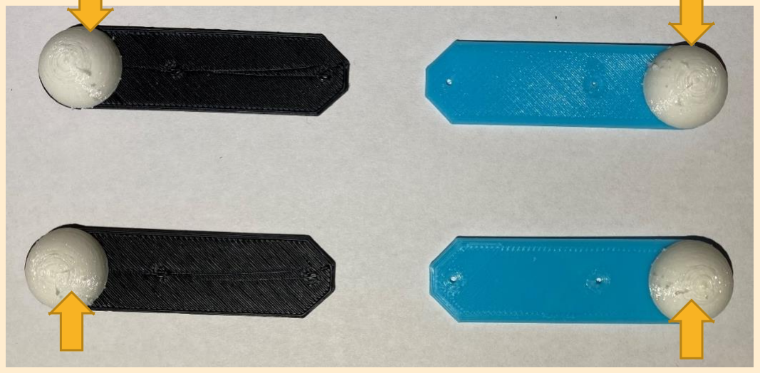
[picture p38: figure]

3D Parts
- 3__all_miniToe_rubber.stl (https://github.com/alex8411/minicat/blob/main/3D_printing/STL/3__all_miniToe_rubber.stl)
- 9__1_miniShank_Batch1.stl (https://github.com/alex8411/minicat/blob/main/3D_printing/STL/9__1_miniShank_Batch1.stl)
- 9__1_miniShank_Batch2.stl (https://github.com/alex8411/minicat/blob/main/3D_printing/STL/9__1_miniShank_Batch2.stl)
- 9__1_miniShank_Batch3.stl (https://github.com/alex8411/minicat/blob/main/3D_printing/STL/9__1_miniShank_Batch3.stl)
- 9__1_miniShank_Batch4.stl (https://github.com/alex8411/minicat/blob/main/3D_printing/STL/9__1_miniShank_Batch4.stl)

4x Screws M2*5
- https://www.amazon.de/gp/product/B07RYLM9N2/ref=ppx_yo_dt_b_search_asin_title?ie=UTF8&psc=1

# MINICAT ASSEMBLY

# STEP1.2: FEET & SERVO-HOLDERS

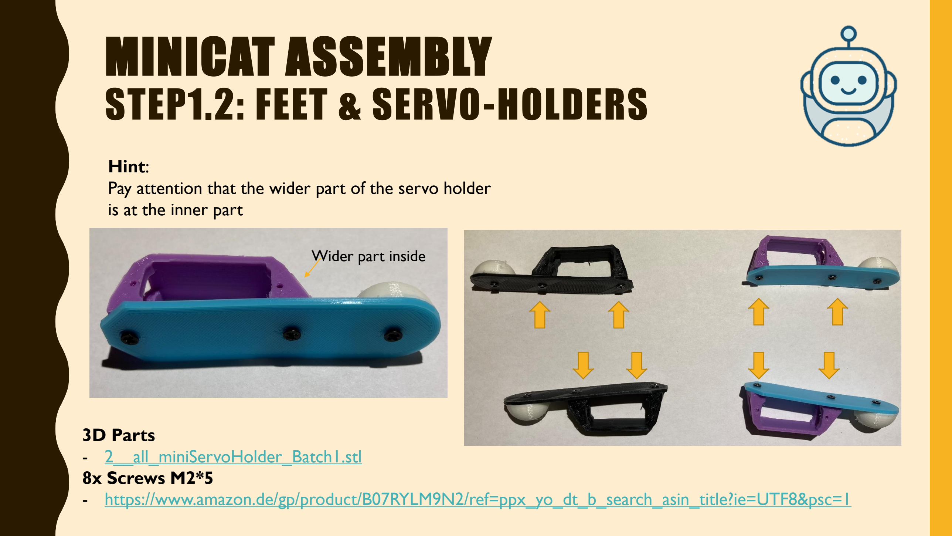
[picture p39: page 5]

3D Parts
- 2__all_miniServoHolder_Batch1.stl (https://github.com/alex8411/minicat/blob/main/3D_printing/STL/2__all_miniServoHolder_Batch1.stl)
8x Screws M2*5
- https://www.amazon.de/gp/product/B07RYLM9N2/ref=ppx_yo_dt_b_search_asin_title?ie=UTF8&psc=1

Hint:
Pay attention that the wider part of the servo holder is at the inner part

Wider part inside

# MINICAT ASSEMBLY

# STEP1.3: FEET, SERVO-HOLDERS & SERVOS

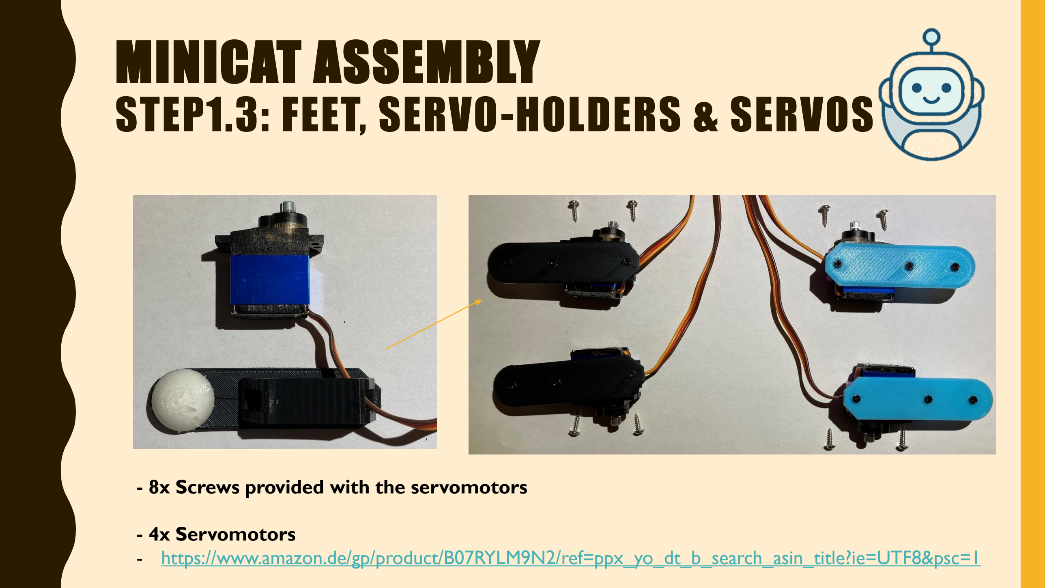
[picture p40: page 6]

- 8x Screws provided with the servomotors
- 4x Servomotors
- https://www.amazon.de/gp/product/B07RYLM9N2/ref=ppx_yo_dt_b_search_asin_title?ie=UTF8&psc=1

# MINICAT ASSEMBLY

# STEP2.1: THIGHS, SERVO-ARMS, SPRINGS

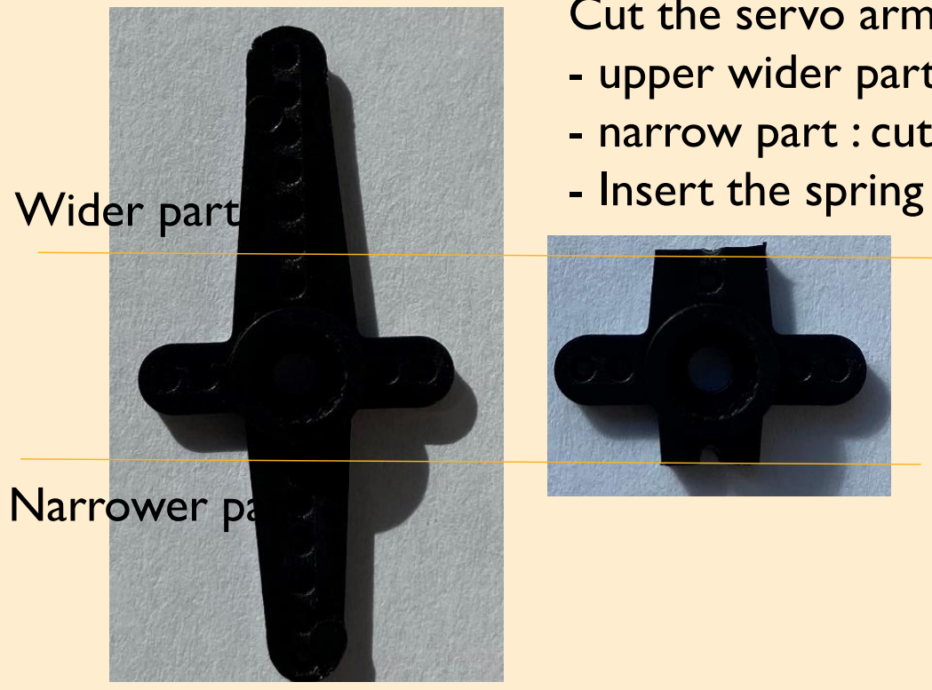
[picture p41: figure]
Wider part; - Insert the spring; Narrower part

3D Parts
- 1__all_miniThigh.stl (https://github.com/alex8411/minicat/blob/main/3D_printing/STL/1__all_miniThigh.stl)

8x Servo arms provided w/ the servomotors
8x Springs 6,5x10mm
- „McDrill“ https://www.amazon.fr/gp/product/B00GN3BJT4/ref=ppx_yo_dt_b_search_asin_image?ie=UTF8&psc=1

Hint:
Cut the servo arm as following:
- upper wider part : cut in the middle of 2d hole
- narrow part : cut in the middle of 1st hole

# MINICAT ASSEMBLY

# STEP2.2: THIGHS & FEET

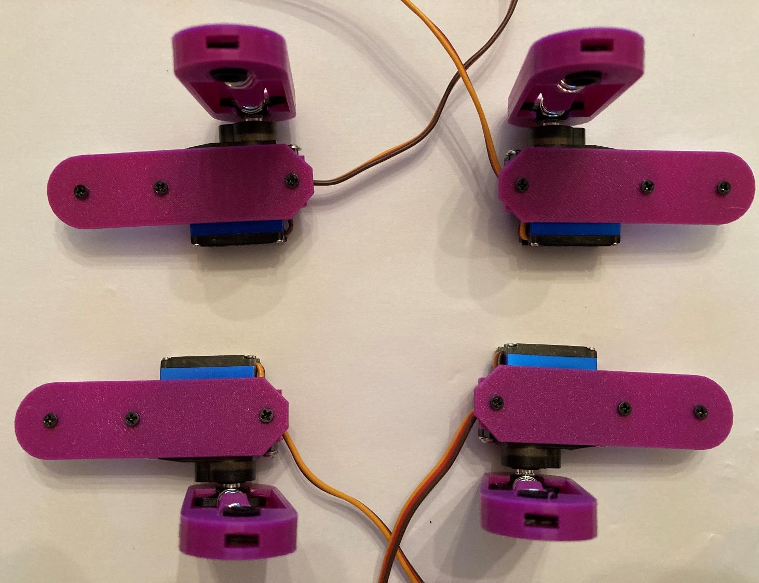
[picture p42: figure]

Hint:
Connect the thighs to the feets as shown on the picture
without screwing them

# MINICAT ASSEMBLY

# STEP3.1: BODY STRUCTURE

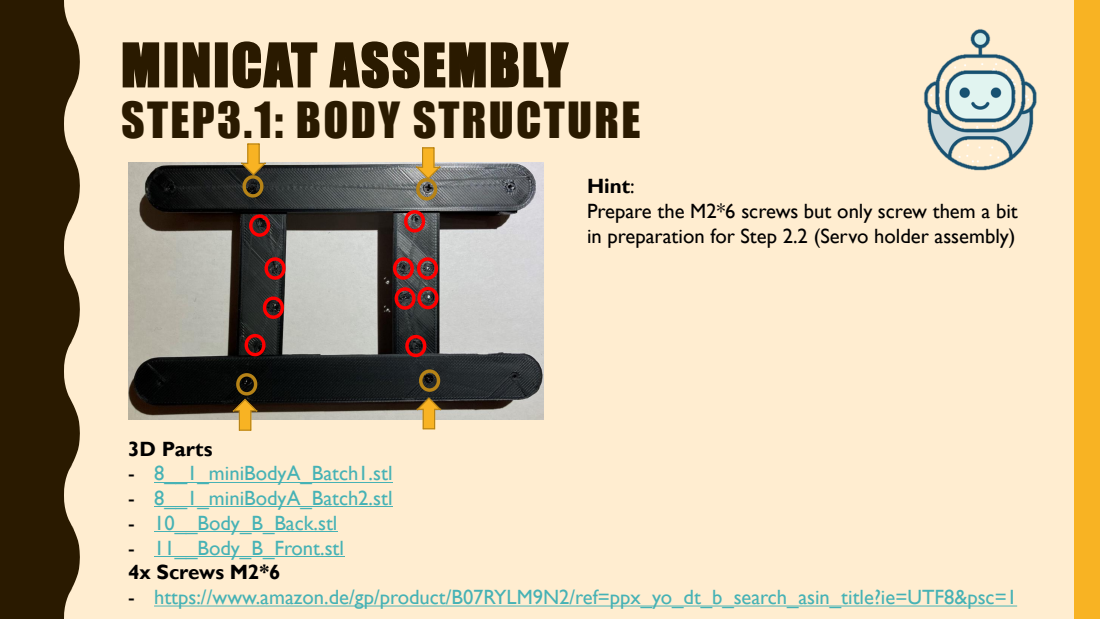
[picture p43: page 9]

Hint:
Prepare the M2*6 screws but only screw them a bit
in preparation for Step 2.2 (Servo holder assembly)

3D Parts
- 8__1_miniBodyA_Batch1.stl (https://github.com/alex8411/minicat/blob/main/3D_printing/STL/8__1_miniBodyA_Batch1.stl)
- 8__1_miniBodyA_Batch2.stl (https://github.com/alex8411/minicat/blob/main/3D_printing/STL/8__1_miniBodyA_Batch2.stl)
- 10__Body_B_Back.stl (https://github.com/alex8411/minicat/blob/main/3D_printing/STL/10__Body_B_Back.stl)
- 11__Body_B_Front.stl (https://github.com/alex8411/minicat/blob/main/3D_printing/STL/11__Body_B_Front.stl)
4x Screws M2*6
- https://www.amazon.de/gp/product/B07RYLM9N2/ref=ppx_yo_dt_b_search_asin_title?ie=UTF8&psc=1

# MINICAT ASSEMBLY

# STEP3.2: BODY & SERVO-HOLDERS

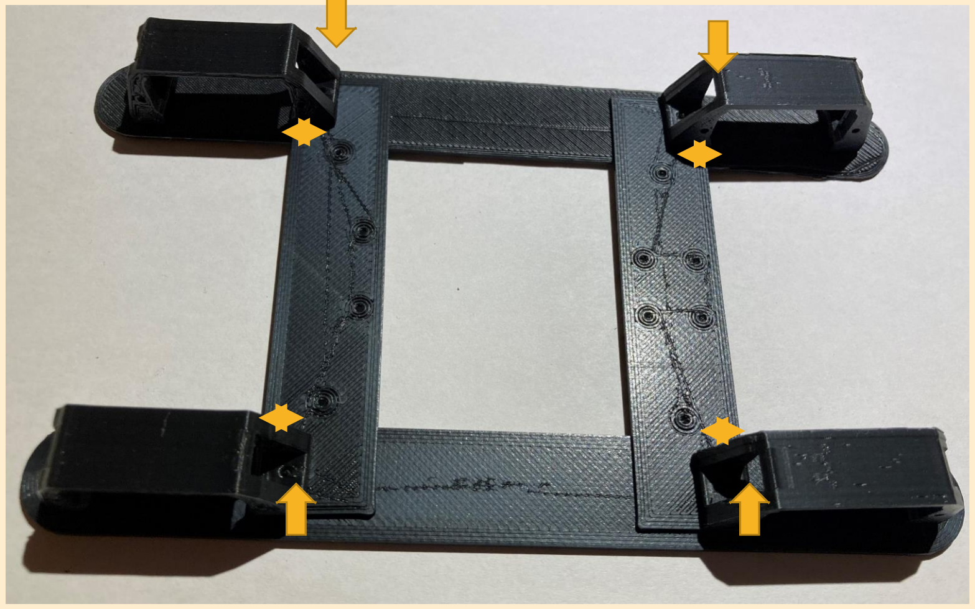
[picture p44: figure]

3D Parts
- 2__all_miniServoHolder_Batch2.stl (https://github.com/alex8411/minicat/blob/main/3D_printing/STL/2__all_miniServoHolder_Batch2.stl)

Hint:

- Now screw completely the M2*6 screws to make sure the 4x Servo holders are fixed at their internal side
- Pay attention that the wider part of the servo holder is at the inner part

# MINICAT ASSEMBLY

# STEP3.3: BODY TOP & SERVO-HOLDERS

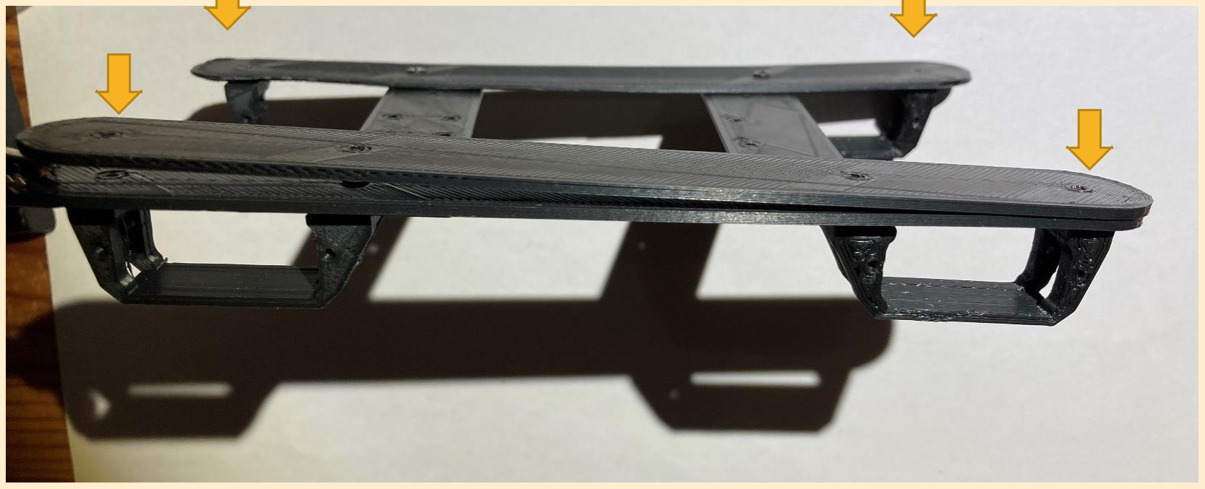
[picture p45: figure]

3D Parts
- 8__1_miniBodyA_Batch3.stl (https://github.com/alex8411/minicat/blob/main/3D_printing/STL/8__1_miniBodyA_Batch3.stl)
- 8__1_miniBodyA_Batch4.stl (https://github.com/alex8411/minicat/blob/main/3D_printing/STL/8__1_miniBodyA_Batch4.stl)
4x Screws M2*7
- https://www.amazon.de/gp/product/B07RYLM9N2/ref=ppx_yo_dt_b_search_asin_title?ie=UTF8&psc=1

Hint:
Now you can screw at the outer side of the 4x servo holders
by adding the 2x additional BodyA structures on top of the 2x existing ones

# MINICAT ASSEMBLY

# STEP3.4: BODY & SERVO-MOTORS

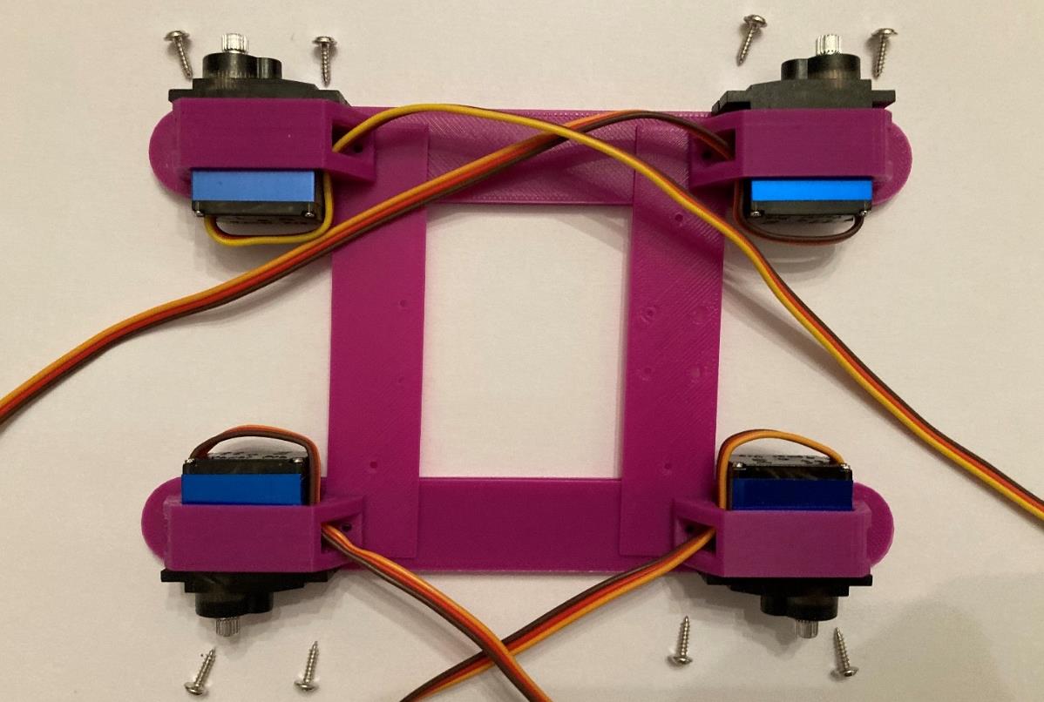
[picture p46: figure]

- 4x Servomotors
https://www.amazon.de/gp/product/B07RYLM9N2/ref=ppx_yo_dt_b_search_asin_title?ie=UTF8&psc=1
- 8x Screws provided with the servomotors https://www.amazon.de/gp/product/B07RYLM9N2/ref=ppx_yo_dt_b_search_asin_title?ie=UTF8&psc=1

Hint:
Pay attention to put the servomotors axis at the outside

# MINICAT ASSEMBLY

# STEP3.5: BODY & LEGS

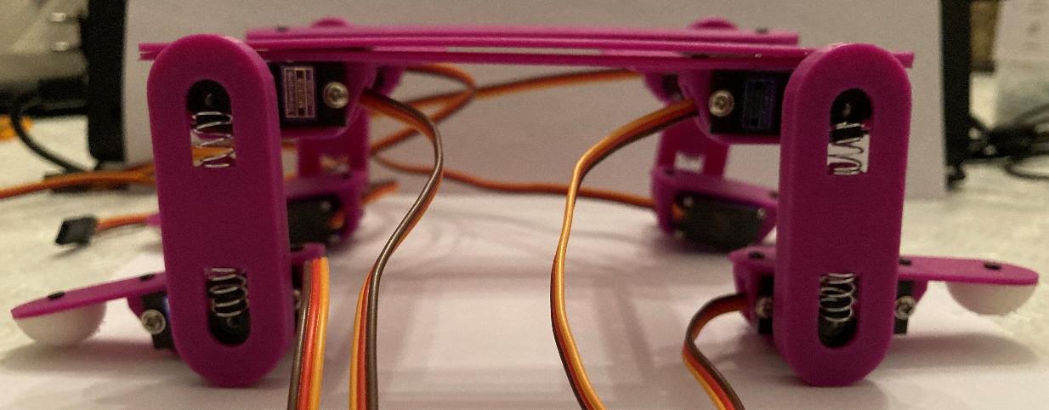
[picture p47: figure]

Hint:
connect only the Legs to the body servomotors axis without screwing them (as calibration still needed later, esp. you do not know yet where the servo +/- 0 angle is)

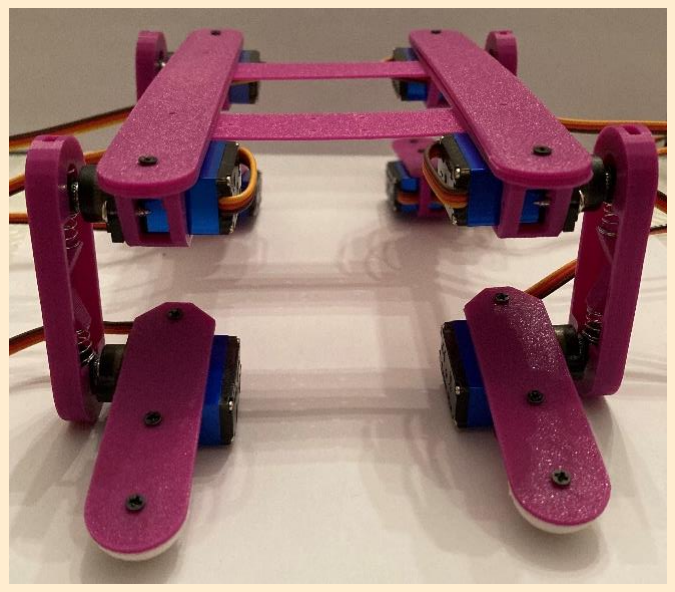
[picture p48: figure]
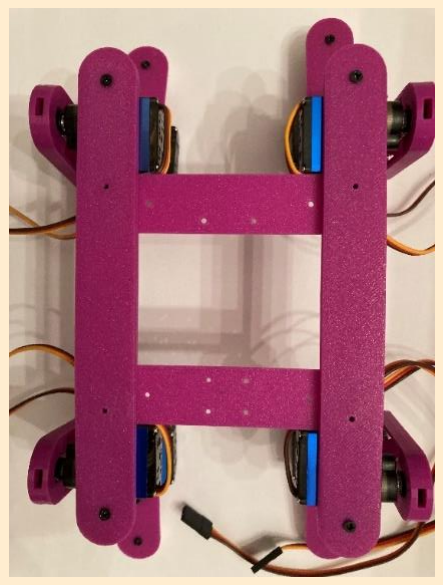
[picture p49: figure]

# MINICAT ASSEMBLY

# STEP4.1: BATTERIES HOLDER & SUPPORT

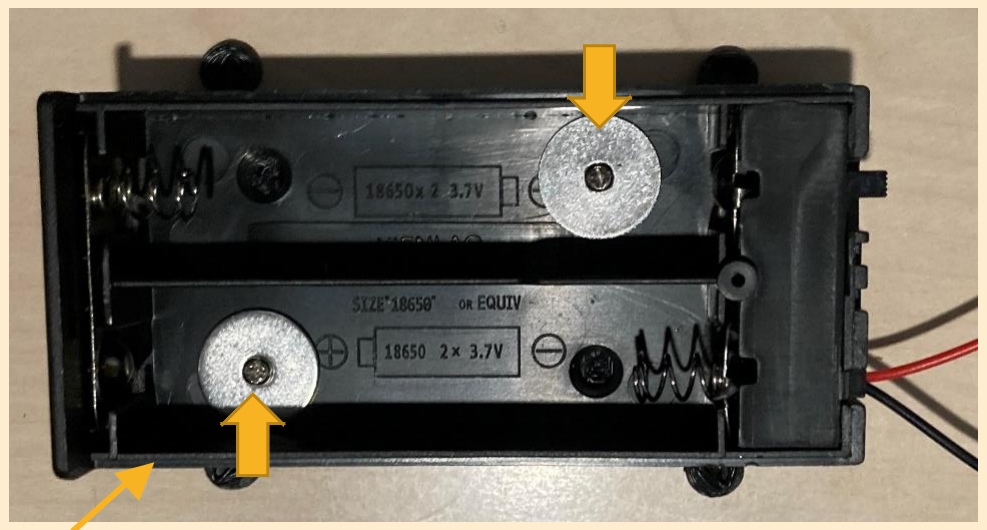
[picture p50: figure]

3D Parts
- 4__Battery_holder_FINAL_STL.stl (https://github.com/alex8411/minicat/blob/main/3D_printing/STL/4__Battery_holder_FINAL_STL.stl)
1x 18650 batteries holder with case :


- https://www.aliexpress.com/item/32901150833.html?spm=a2g0s.9042311.0.0.27424c4dfSUBPq
2x Screws M2*8
- https://www.amazon.de/gp/product/B07RYLM9N2/ref=ppx_yo_dt_b_search_asin_title?ie=UTF8&psc=1 2x Gasket M3 (13 outside diameter)
Batteries holder | Batteries holder support

# MINICAT ASSEMBLY

# STEP4.2: BATTERIES HOLDER & BODY


4x Screws M2*7


- https://www.amazon.de/gp/product/B07RYLM9N2/ref=ppx_yo_dt_b_search_asin_title?ie=UTF8&psc=1 Support between battery holder support and body structure
- 5__miniCircuit.stl (https://github.com/alex8411/minicat/blob/main/3D_printing/STL/5__miniCircuit.stl)

Hint:
1- Screw the 4x M2*7 screws first in the batteries holder support

Hint:
2- Screw the 4x M2*7 screws through the batteries holder support and intermediate support

Intermediate support

# MINICAT ASSEMBLY

# STEP4.3: BATTERIES HOLDER & BODY & PCB


Hint:
- the 4x M2x10 go
through the PCB first
AND
then through
the intermediate support part

Electronic Parts
- MiniCat_2.0_PCB_1_0.fzz (https://github.com/alex8411/minicat/blob/main/PCB/MiniCat_2.0_PCB_1_0.fzz)
4x Screws M2*10
- https://www.amazon.de/gp/product/B07RYLM9N2/ref=ppx_yo_dt_b_search_asin_title?ie=UTF8&psc=1

# MINICAT ASSEMBLY

# STEP5: PCB & ELECTRONIC MODULES


Electronic Parts
- MiniCat_2.0_PCB_1_0.fzz (https://github.com/alex8411/minicat/blob/main/PCB/MiniCat_2.0_PCB_1_0.fzz)


# SOFTWARE INTEGRATION

# STEP6: FLASH SOFTWARE & PLAY !

Forwards; Backwards; Positions; Software: - minicat_basic

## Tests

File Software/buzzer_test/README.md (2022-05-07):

Test the buzzer (a melody will be played).

CAUTION: the servo driver board should be connected for the Buzzer to be supplied as the buzzer supply crosses the servo driver header.

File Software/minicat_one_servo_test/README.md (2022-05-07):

Adding minicat_one_servo_test.ino to test the servo driver board and 1x Servomotor 

This Software will move the servo axis between 10 and 30 degrees.

Check the "Tools / Serial Monitor" to see the angle commands.

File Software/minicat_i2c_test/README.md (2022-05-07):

Adding minicat_i2c_test.ino to test the I2C communication and Master (Arduino) - Slaves (Servo driver board and Gyroscope) present

After uploading the Sketch you can start the "Tools / Serial Monitor" (57600 baud)

the following result should be shown if all I2C devices are recognised:

Scanning...
I2C device found at address 0x40  ! (Servos driver board, I2C slave)
I2C device found at address 0x68  ! (Gyro board, I2C slave)
I2C device found at address 0x70  ! (Arduino board, I2C master)
done

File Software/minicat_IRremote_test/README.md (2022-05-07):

- adding IRremote test Software based on IRremote library (need to ne installed in your Arduino IDE : Tools/Manage Libraries “IRremote”)
- allow you to send Infrared commands with the remote control to your Arduino via the IR recweiver module
- after uploading the sketch, check the "Tools / Serial Monitor" to see the commands received by the Arduino

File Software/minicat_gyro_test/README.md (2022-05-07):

Minicat_gyro_test for testing the MPU6050 Gyroscope feature.

After upload of the sketch:
- start the Arduino IDE "Tools / serial monitor"
- make sure you set the serial link speed to "57600 baud" (by default 9600 baud)
- the yaw/pitch/roll angles ("ypr") of the robot as well as its x, y, z accelerations ("accreal") should be displayed in the console

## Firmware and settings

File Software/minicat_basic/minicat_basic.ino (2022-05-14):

/*

======================== ATELIER ROBOTIQUE : CatMini ========================
==                           Programme principal                           ==
==                          Faire bouger MiniCat                           ==
=============================================================================

Ecrit par Rongzong Li, Petoi 
Modifié et commenté par Lilie Boizumault, QI Informatique 
2020 
Edited by Alexis Veynachter, 2021-2022


*/


// Définition de raccourcis 

#define SPT(s) Serial.print(s)
#define SPTL(s) Serial.println(s)
#define SPTF(s) Serial.print(F(s))
#define SPLF(s) Serial.println(F(s))



// Variables pour le module MPU6050 
// ---------------------------------------------------------------------------------

#include "I2Cdev.h"
#include "MPU6050_6Axis_MotionApps20.h"

MPU6050 mpu;



bool dmpReady = false;  
uint8_t mpuIntStatus;  
uint8_t devStatus;     
uint16_t packetSize;    
uint16_t fifoCount;     
uint8_t fifoBuffer[64]; 


Quaternion q;           
VectorFloat gravity;   
float ypr[3], yprLag[2][3];        
bool overFlow = false;



volatile bool mpuInterrupt = false;     
void dmpDataReady() {
  mpuInterrupt = true;
}

// ---------------------------------------------------------------------------------



// Définition des fonctions beep() et melody() (comme vu lors du montage)

// ---------------------------------------------------------------------------------

#include <EEPROM.h> // bibliothèque pour accéder à la mémoire EEPROM 

#define BUZZER 4
#define MELODY 1023
void beep(byte note, float duration = 10, int pause = 0, byte repeat = 1 ) {
  if (note == 0) {
    analogWrite(BUZZER, 0);
    delay(duration);
    return;
  }
  int freq = 220 * pow(1.059463, note);
  float period = 1000000.0 / freq / 2.0;
  for (byte r = 0; r < repeat; r++) {
    for (float t = 0; t < duration * 1000; t += period * 2) {
      analogWrite(BUZZER, 150);      
      delayMicroseconds(period);         
      analogWrite(BUZZER, 0);     
      delayMicroseconds(period);          
    }
    delay(pause);
  }
}
void playMelody(int start) {  // on a stocké la mélodie dans l'EEPROM 
  byte len = (byte)EEPROM.read(start) / 2;
  for (int i = 0; i < len; i++)
    beep(EEPROM.read(start - 1 - i), 1000 / EEPROM.read(start - 1 - len - i), 100);
}

// ---------------------------------------------------------------------------------



// Définition des actions à associer à chaque bouton de la télécommande IR 

// ---------------------------------------------------------------------------------


#include "IRremote.h"
int receiver = 5; 

IRrecv irrecv(receiver);     
decode_results results;      

//AV: below the IR remote control sent commands
//AV: if a new position/movement is needed from the existing list (see in modes.h), you need to associate the abbreviation of position/movement you want to add in the case list below
//AV: for example the position "pee" is currently not associated with any of the remote control key listed below

String translateIR() 
{                                     
  switch (results.value) { // cette fois l'action est de renvoyer l'abréviation de la 
    // posture ou du mouvement demandé


    
                 //abbreviation of gaits      key on IR remote                gait/posture names
    case 0xFF18E7: return (F("vt"));        //Serial.println(" FORWARD");   //stepping on spot, "mark time"
    case 0xFF10EF: return (F("sit"));       //Serial.println(" LEFT");      //sit
    case 0xFF38C7: return (F("bd"));        //Serial.println(" -OK-");      //bound
    case 0xFF5AA5: return (F("balance"));   //Serial.println(" RIGHT");     //standing
    case 0xFF4AB5: return (F("d"));         //Serial.println(" REVERSE");   //shut down servos
    case 0xFFA25D: return (F("trL"));       //Serial.println(" 1");         //trot left
    case 0xFF629D: return (F("tr"));        //Serial.println(" 2");         //trot 
    case 0xFFE21D: return (F("trR"));       //Serial.println(" 3");         //trot right
    case 0xFF22DD: return (F("wkL"));       //Serial.println(" 4");         //walk left
    case 0xFF02FD: return (F("wk"));        //Serial.println(" 5");         //walk 
    case 0xFFC23D: return (F("wkR"));       //Serial.println(" 6");         //walk right
    case 0xFFE01F: return (F("crL"));       //Serial.println(" 7");         //crawl left
    case 0xFFA857: return (F("cr"));        //Serial.println(" 8");         //crawl
    case 0xFF906F: return (F("crR"));       //Serial.println(" 9");         //crawl right
    case 0xFF6897: return (F("bkL"));       //Serial.println(" *");         //back left
    case 0xFF9867: return (F("bk"));        //Serial.println(" 0");         //back
    case 0xFFB04F: return (F("bkR"));       //Serial.println(" #");         //back right
    case 0xFFFFFFFF: return (""); //Serial.println(" REPEAT");

    default:
      return ("");                      //Serial.println("null");
  }
}

// ---------------------------------------------------------------------------------



// Définition des constantes pour les servomoteurs 

// ---------------------------------------------------------------------------------

#define DOF 16

#include <Wire.h>
#include <Adafruit_PWMServoDriver.h>


Adafruit_PWMServoDriver pwm = Adafruit_PWMServoDriver();

#define SERVOMIN  150 
#define SERVOMAX  600 
#define BOUND 1/8
#define RANGE (SERVOMAX - SERVOMIN)


int8_t servoCalibs[DOF] = {}; // variable pour stocker la position de référence en degrés
char currentAng[DOF] = {}; // variable pour stocker la position actuelle de chaque servomoteur 


// Définition des tolérances de rotation (roulis, tangage, lacet) sur chaque articulation
#define FLAT 5
#define panF 1 / 2.0
#define tF 1.0
#define sXF 2
#define sYF 1/4.0
#define uF 0.8
#define dF -0.8
float coeff[16][2] = {
  { -panF, 0}, {0, -tF}, {0, 0}, {0, 0},
  {sXF, -sYF}, { -sXF, -sYF}, { -sXF, sYF}, {sXF, sYF},
  { uF, 1}, { -uF, 1}, { -uF , -1 }, { uF , -1 },
  { dF, dF}, { -dF, dF}, { -dF, -dF}, { dF, -dF}
};

// ---------------------------------------------------------------------------------


int calibratedDuty0[DOF]; // variable pour stocker la position de référence en longeur de pulsation

#include "modes.h" // on inclut le fichier de définition des postures et mouvements 


// Définition des fonctions pour écrire et lire dans l'EEPROM

// ---------------------------------------------------------------------------------

#define PIN 0  // définition des emplacements de stockage des variables 
#define CALIB 16
#define MIDSHIFT 32
#define ROTDIRECTION 48
#define RANGERATIO 64
#define MPUCALIB 80



void EEPROMWriteInt(int p_address, int p_value) // écriture d'une variable à une certaine 
// adresse de l'EEPROM
{
  byte lowByte = ((p_value >> 0) & 0xFF);
  byte highByte = ((p_value >> 8) & 0xFF);
  EEPROM.update(p_address, lowByte);
  EEPROM.update(p_address + 1, highByte);
}


int EEPROMReadInt(int p_address) // lecture de la valeur d'une variable stockée à 
// une certaine adresse de l'EEPROM
{
  byte lowByte = EEPROM.read(p_address);
  byte highByte = EEPROM.read(p_address + 1);
  return ((lowByte << 0) & 0xFF) + ((highByte << 8) & 0xFF00);
}


byte pin(byte idx) {  // retourne la valeur du pin sur lequel est branché le servomoteur
// numéro "idx"
  return (byte)EEPROM.read(PIN + idx);
}


int8_t middleShift(byte idx) { // retourne la valeur de middleshift correspondant au 
// servomoteur numéro "idx"
  return (int8_t)EEPROM.read( MIDSHIFT + idx);
}


byte rangeRatio(byte idx) { // retourne la valeur de rangeRatio correspondant au 
// servomoteur numéro "idx"
  return (byte)EEPROM.read(RANGERATIO + idx);
}


int8_t rotationDirection(byte idx) { // retourne la valeur de rotationDirection 
// correspondant au servomoteur numéro "idx"
  return (int8_t)EEPROM.read(ROTDIRECTION + idx);
}


int8_t servoCalib(byte idx) { // retourne la valeur de l'offset sur la position de  
// référence correspondant au servomoteur numéro "idx"
  return (int8_t)EEPROM.read( CALIB + idx);
}


void saveCalib(int8_t *var) { // écriture des bonnes valeurs d'offset pour la position
// de référence => sauvegarde de l'étalonnage 
  for (byte i = 0; i < DOF; i++) {
    EEPROM.update(CALIB + i, var[i]);
    calibratedDuty0[i] = SERVOMIN + RANGE / 2 + float(middleShift(i) + var[i]) * RANGE * rotationDirection(i) / rangeRatio(i);
  }
}

// ---------------------------------------------------------------------------------


// Définition des fonctions de mouvement

// ---------------------------------------------------------------------------------

void calibratedPWM(byte i, int dt) { // fonction qui règle le servomoteur i à l'ange dt
  char duty = max(-128, min(127, dt)); // on force l'angle dt à être entre -128 et 127 degrés 
  if (i > 3 && i < 8) // si l'indice du servomoteur est entre 4 et 7
    duty = max(-5, duty); // l'angle doit être plus grand que -5 degrés
  currentAng[i] = duty; // stockage de la valeur de l'angle pour le servomoteur i 
  dt = calibratedDuty0[i] + float(duty) * RANGE * rotationDirection(i) / rangeRatio(i); // conversion en longueur de pulsation
  dt = max(SERVOMIN + RANGE / 2 * BOUND, min(SERVOMAX - RANGE / 2 * BOUND, dt)); // on contraint la longeur de pulsation
  // à être entre les bonnes valeurs 
  pwm.setPWM(pin(i), 0, dt); // commande du servomoteur 
}


void allCalibratedPWM(char * dutyAng) { // fonction qui place tous les servomoteurs 
  // aux bons angles 
  for (byte i = 0; i < DOF; i++) {
    calibratedPWM(i, dutyAng[i]); // envoi de chaque servomoteur à l'angle voulu 
  }
}


void printList(char * arr, byte len = DOF) { // affiche les valeurs d'une liste sur le moniteur 
  // série
  for (byte i = 0; i < len; i++) {
    SPT(int(arr[i]));
    SPT('\t');
  }
  SPTL();
}


void transform( char * target, byte offset = 0, float speedRatio = 0.5) { // fonction qui 
  // place les servomoteurs aux angles cibles, en prenant en compte la position actuelle
  // Indique de combien chaque servomoteur doit tourner pour se placer à l'angle voulu

  char *diff = new char[DOF - offset], maxDiff = 0; // initialisation de la variable diff
  
  for (byte i = offset; i < DOF; i++) { // pour chaque servomoteur 
    diff[i - offset] =   currentAng[i] - target[i - offset]; // on calcule la différence
    // entre l'angle actuel et l'angle voulu  
    maxDiff = max(maxDiff, abs( diff[i - offset])); // maxDiff devient une valeur positive (0 ou plus) 
  }
  
  byte steps = byte(round(maxDiff / 3.0/*degreeStep*/ / speedRatio)); // conversion de la différence 
  // en nombre de "pas" pour la rotation 
  for (byte s = 0; s < steps; s++) // pour chaque pas de rotation 
    for (byte i = offset; i < DOF; i++) { // pour chaque servomoteur 
      char duty = (target[i - offset] + (1 + cos(M_PI * s / steps)) / 2 * diff[i - offset]); // calcul de l'angle 
      // à envoyer 
      calibratedPWM(i,  duty); // Envoi au servomoteur i 
    }
  delete [] diff; // effacer diff
  
}


void shutServos() { // fonction pour éteindre les servomoteurs 
  delay(250);
  for (byte i = 0; i < DOF; i++) {
    pwm.setPWM(i, 0, 4096);
  }
}


int8_t idxOfGait(const char * gait) { // retourne l'indice de la posture ou du mouvement 
  // demandé
  for (byte i = 0; i < sizeof(gaits) / sizeof(char*); i++) // on parcourt la liste 
  // des mouvements  et postures
    if (!strcmp(gaits[i], gait)) // quand on trouve le bon nom dans la liste 
      return i; // on retourne i 
  return -1;
}


//AV: target angles for the servomotors are taken from a certain position or movement target which is sent by the remote control or terminal :

int pgmCpy(char * dutyAng, const char * gait) { // fonction qui copie dans dutyAng les angles 
  // voulus pour réaliser une certaine posture (ou mouvement) 
  dutyAng--;
  strcpy_P(dutyAng, (char*)pgm_read_word(&(gaits_table[idxOfGait(gait)]))); // on cherche l'indice 
  // de la posture (ou mouvement)dans la liste des postures 
  // on récupère le contenu (angles voulus) dans le fichier modes.h
  // on copie ces angles dans dutyAng
  int period = dutyAng[0]; // on récupère le nombre de postures ( 0 -> posture fixe, sinon -> mouvement)
  dutyAng++;
  return period;
}

// AV: this is where the gyroscope latest measurement is taken in account to adjust the balance of the robot : 

int adjust(int i) { // calculer un coefficient de rotation, pour l'équilibre
  if (i>7)
    return coeff[i][0] * ypr[2] * 180 / M_PI + coeff[i][1] * ypr[1] * 180 / M_PI;
  else
    return coeff[i][0] * ypr[2] * 180 / M_PI + coeff[i][1] * ypr[1] * 180 / M_PI;
}


// ---------------------------------------------------------------------------------


// Initialisation des variables nécéssaires 
int t = 0;
int tPeriod = 1;
byte hold = 0;
byte offset;
char token;
#define CMD_LEN 10
char lastCmd[CMD_LEN] = {};



/* =================================================================================
 * ==                                                                             ==
 * ==                           SETUP - INITIALISATION                            == 
 * ==                                                                             == 
 * =================================================================================
 */


void setup() {

// Initialisation MPU6050

// ---------------------------------------------------------------------------------
 
#if I2CDEV_IMPLEMENTATION == I2CDEV_ARDUINO_WIRE
  Wire.begin();
  TWBR = 24; 
#elif I2CDEV_IMPLEMENTATION == I2CDEV_BUILTIN_FASTWIRE
  Fastwire::setup(400, true);
#endif

  Serial.begin(57600);
  Serial.setTimeout(10);
  while (!Serial);
  while (Serial.available() && Serial.read()); 
  delay(100);
  SPLF("* Starting *");
  SPLF("Initializing I2C");
  mpu.initialize();
  SPLF("Testing connections...");
  Serial.println(mpu.testConnection() ? F("MPU successful") : F("MPU failed"));
  Serial.println(F("Initializing DMP..."));
  //devStatus = mpu.dmpInitialize();//AV, RoboticsForMakers: commenting this line, minicat_basic.ino software not running stable with this line
  mpu.setZAccelOffset(EEPROMReadInt(MPUCALIB + 4));
  mpu.setXGyroOffset(EEPROMReadInt(MPUCALIB + 6));
  mpu.setYGyroOffset(EEPROMReadInt(MPUCALIB + 8));
  mpu.setZGyroOffset(EEPROMReadInt(MPUCALIB + 10));
  
  if (devStatus == 0) {
    Serial.println(F("Enabling DMP..."));
    mpu.setDMPEnabled(true);
    Serial.println(F("Enabling interrupt detection"));
    attachInterrupt(0, dmpDataReady, RISING);
    mpuIntStatus = mpu.getIntStatus();
    Serial.println(F("DMP ready!"));
    dmpReady = true;
    packetSize = mpu.dmpGetFIFOPacketSize();
  } else {
    Serial.println(F("DMP failed (code "));
    SPT(devStatus);
    SPLF(")");
  }

// ---------------------------------------------------------------------------------
  

  if (WalkingDOF == 8)
  {
    pinMode(BUZZER, OUTPUT);
    playMelody(MELODY); // Musique d'initialisation 
    Serial.println("DEBUG : Init Melody played"); //AV: DEBUG : check if we reach this line
    
  }

  {
    irrecv.enableIRIn(); // Initialisation pour l'IR
    Serial.println("DEBUG : Init IR done"); //AV: DEBUG : check if we reach this line
  }

  // Initialisation pour les servomoteurs
  { pwm.begin();
    pwm.setPWMFreq(60);  
    delay(200);
    char cmd[CMD_LEN] = {};
   

    strcpy(lastCmd, "rest");
    pgmCpy(dutyAng, "rest"); // on charge les angles de la position "rest" dans dutyAng
    
    for (byte i = 0; i < DOF; i++) {
      servoCalibs[i] = servoCalib(i); // Stockage des valeurs des positions de références (en degrés)
      calibratedDuty0[i] =  SERVOMIN + RANGE / 2 + float(middleShift(i) + servoCalibs[i]) * RANGE  * rotationDirection(i) / rangeRatio(i);
      // Stockage des valeurs des positions de références (en longueur de pulsation)
      calibratedPWM(i, dutyAng[i]); // On place les servomoteurs aux bons angles pour la position "rest"
    }
   
    shutServos(); // on éteint les servomoteurs 
    token = 'd'; 
    Serial.println("DEBUG : Init Servos done"); //AV: DEBUG : check if we reach this line
  }
  beep(30);
}

/* =================================================================================
 * ==                                                                             ==
 * ==                           LOOP - BOUCLE PRINCIPALE                          == 
 * ==                                                                             == 
 * =================================================================================
 */



void loop() {
  
// MPU6050

// ---------------------------------------------------------------------------------
  {
    if (!dmpReady) return;
    Serial.println("DEBUG : DMP=MPU init did NOT fail"); //AV: DEBUG : check if we reach this line
    while (!mpuInterrupt && fifoCount < packetSize) ;
    
    mpuInterrupt = false;
    mpuIntStatus = mpu.getIntStatus();
    fifoCount = mpu.getFIFOCount();

    if ((mpuIntStatus & 0x10) || fifoCount == 256) { //1024) {
      mpu.resetFIFO();
      overFlow = true;
    }
    else if (mpuIntStatus & 0x02) {
      while (fifoCount < packetSize) fifoCount = mpu.getFIFOCount();

      mpu.getFIFOBytes(fifoBuffer, packetSize);
      fifoCount -= packetSize;
      mpu.dmpGetQuaternion(&q, fifoBuffer);
      mpu.dmpGetGravity(&gravity, &q);
      mpu.dmpGetYawPitchRoll(ypr, &q, &gravity);
    }
    if (overFlow) {
      for (byte g = 0; g < 3; g++) {
        ypr[g] = yprLag[0][g];
        yprLag[1][g] = yprLag[0][g];
      }
      overFlow = false;
    }
    else {
      for (byte g = 0; g < 3; g++) {
        float temp = ypr[g];
        ypr[g] = yprLag[0][g];
        yprLag[0][g] = yprLag[1][g];
        yprLag[1][g] = temp;
      }
    }
  }

// ---------------------------------------------------------------------------------
  
  for (byte i = 1; i < 3; i++) // on convertit les mesures du gyroscope en angles (degrés)
    ypr[i] = ((ypr[i] > 0) - (ypr[i] < 0)) * max(fabs(ypr[i]) - FLAT*M_PI/180.0, 0);
  ypr[2] = -ypr[2];

  char cmd[CMD_LEN] = {};
  byte newCmd = 0;


// block "accident" 
  
// ---------------------------------------------------------------------------------

  if (fabs(ypr[1] * 180 / M_PI) > 60) { // Si l'angle de rotation du robot est trop important 
    if (!hold) {
      token = 'p';
      strcpy(cmd, ypr[1] * 180 / M_PI > 60 ? "lifted" : "dropped"); // c'est qu'il est tenu en l'air (lifted)
      // ou tombé (dropped)
      newCmd = 1;
    }
    hold = 10;
  }
  // Dans ce cas : se relever 
  else if (hold ) {
    if (hold == 10) {
      token = 'p';
      strcpy(cmd, "balance"); // le robot se met debout 
      newCmd = 1;
    }
    hold --;
    if (!hold) {
      char temp[CMD_LEN];
      strcpy(temp, cmd);
      strcpy(cmd, lastCmd);
      strcpy(lastCmd, temp); // stockage de la commande "balance" dans la mémoire (variable "lastCmd")
      newCmd = 1;
    }
  }

// ---------------------------------------------------------------------------------

// Block de commande
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

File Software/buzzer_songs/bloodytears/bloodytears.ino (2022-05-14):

/* 
  Bloody Tears from Castlevania II
  Connect a piezo buzzer or speaker to pin 11 or select a new pin.
  More songs available at https://github.com/robsoncouto/arduino-songs                                            
                                              
                                              Robson Couto, 2019
*/

#define NOTE_B0  31
#define NOTE_C1  33
#define NOTE_CS1 35
#define NOTE_D1  37
#define NOTE_DS1 39
#define NOTE_E1  41
#define NOTE_F1  44
#define NOTE_FS1 46
#define NOTE_G1  49
#define NOTE_GS1 52
#define NOTE_A1  55
#define NOTE_AS1 58
#define NOTE_B1  62
#define NOTE_C2  65
#define NOTE_CS2 69
#define NOTE_D2  73
#define NOTE_DS2 78
#define NOTE_E2  82
#define NOTE_F2  87
#define NOTE_FS2 93
#define NOTE_G2  98
#define NOTE_GS2 104
#define NOTE_A2  110
#define NOTE_AS2 117
#define NOTE_B2  123
#define NOTE_C3  131
#define NOTE_CS3 139
#define NOTE_D3  147
#define NOTE_DS3 156
#define NOTE_E3  165
#define NOTE_F3  175
#define NOTE_FS3 185
#define NOTE_G3  196
#define NOTE_GS3 208
#define NOTE_A3  220
#define NOTE_AS3 233
#define NOTE_B3  247
#define NOTE_C4  262
#define NOTE_CS4 277
#define NOTE_D4  294
#define NOTE_DS4 311
#define NOTE_E4  330
#define NOTE_F4  349
#define NOTE_FS4 370
#define NOTE_G4  392
#define NOTE_GS4 415
#define NOTE_A4  440
#define NOTE_AS4 466
#define NOTE_B4  494
#define NOTE_C5  523
#define NOTE_CS5 554
#define NOTE_D5  587
#define NOTE_DS5 622
#define NOTE_E5  659
#define NOTE_F5  698
#define NOTE_FS5 740
#define NOTE_G5  784
#define NOTE_GS5 831
#define NOTE_A5  880
#define NOTE_AS5 932
#define NOTE_B5  988
#define NOTE_C6  1047
#define NOTE_CS6 1109
#define NOTE_D6  1175
#define NOTE_DS6 1245
#define NOTE_E6  1319
#define NOTE_F6  1397
#define NOTE_FS6 1480
#define NOTE_G6  1568
#define NOTE_GS6 1661
#define NOTE_A6  1760
#define NOTE_AS6 1865
#define NOTE_B6  1976
#define NOTE_C7  2093
#define NOTE_CS7 2217
#define NOTE_D7  2349
#define NOTE_DS7 2489
#define NOTE_E7  2637
#define NOTE_F7  2794
#define NOTE_FS7 2960
#define NOTE_G7  3136
#define NOTE_GS7 3322
#define NOTE_A7  3520
#define NOTE_AS7 3729
#define NOTE_B7  3951
#define NOTE_C8  4186
#define NOTE_CS8 4435
#define NOTE_D8  4699
#define NOTE_DS8 4978
#define REST 0

// change this to make the song slower or faster
int tempo = 144;

// change this to whichever pin you want to use
int buzzer = 4;

// notes of the moledy followed by the duration.
// a 4 means a quarter note, 8 an eighteenth , 16 sixteenth, so on
// !!negative numbers are used to represent dotted notes,
// so -4 means a dotted quarter note, that is, a quarter plus an eighteenth!!
const PROGMEM int melody[] = {


  // Bloody Tears, from Castlevania II
  // Arranged by Bobby Lee. THe flute part was used 
  // https://musescore.com/user/263171/scores/883296
  
  //B-flat major Bb Eb
  REST, 4, NOTE_G5, 4,
  NOTE_A5, 4, NOTE_AS5, 4,
  NOTE_A5, 4, NOTE_F5, 4,
  NOTE_A5, 4, NOTE_G5, 4,
  REST, 4, NOTE_G5, 4,
  NOTE_A5, 4, NOTE_AS5, 4,
  NOTE_C6, 4, NOTE_AS5, 4,

  NOTE_A5, 4, NOTE_G5, 4, //8
  REST, 4, NOTE_G5, 4,
  NOTE_A5, 4, NOTE_AS5, 4,
  NOTE_A5, 4, NOTE_F5, 4,
  NOTE_A5, 4, NOTE_G5, 4,
  NOTE_D6, 4, REST, 8, NOTE_C6, 8,
  REST, 4, NOTE_AS5, 4,

  NOTE_A5, 4, NOTE_AS5, 8, NOTE_C6, 8, //15
  NOTE_F6, 8, REST, 8, REST, 4,
  NOTE_G5, 16, NOTE_D5, 16, NOTE_D6, 16, NOTE_D5, 16, NOTE_C6, 16, NOTE_D5, 16, NOTE_AS5, 16, NOTE_D5, 16,
  NOTE_A5, 16, NOTE_D5, 16, NOTE_AS5, 16, NOTE_D5, 16, NOTE_A5, 16, NOTE_D5, 16, NOTE_G5, 16, NOTE_D5, 16,
  NOTE_A5, 16, NOTE_D5, 16, NOTE_AS5, 16, NOTE_D5, 16, NOTE_C6, 16, NOTE_D5, 16, NOTE_AS5, 16, NOTE_D5, 16,

  NOTE_A5, 16, NOTE_D5, 16, NOTE_F5, 16, NOTE_D5, 16, NOTE_A5, 16, NOTE_D5, 16, NOTE_G5, 16, NOTE_D5, 16, //20
  NOTE_G5, 16, NOTE_D5, 16, NOTE_D6, 16, NOTE_D5, 16, NOTE_C6, 16, NOTE_D5, 16, NOTE_AS5, 16, NOTE_D5, 16,
  NOTE_A5, 16, NOTE_D5, 16, NOTE_AS5, 16, NOTE_D5, 16, NOTE_A5, 16, NOTE_D5, 16, NOTE_AS5, 16, NOTE_D5, 16,
  NOTE_A5, 16, NOTE_D5, 16, NOTE_AS5, 16, NOTE_D5, 16, NOTE_C6, 16, NOTE_D5, 16, NOTE_AS5, 16, NOTE_D5, 16,
  NOTE_A5, 16, NOTE_D5, 16, NOTE_F5, 16, NOTE_D5, 16, NOTE_A5, 16, NOTE_D5, 16, NOTE_G5, 16, NOTE_D5, 16,

  NOTE_G5, 16, NOTE_D5, 16, NOTE_D6, 16, NOTE_D5, 16, NOTE_C6, 16, NOTE_D5, 16, NOTE_AS5, 16, NOTE_D5, 16, //25
  NOTE_A5, 16, NOTE_D5, 16, NOTE_AS5, 16, NOTE_D5, 16, NOTE_A5, 16, NOTE_D5, 16, NOTE_G5, 16, NOTE_D5, 16,
  NOTE_A5, 16, NOTE_D5, 16, NOTE_AS5, 16, NOTE_D5, 16, NOTE_C6, 16, NOTE_D5, 16, NOTE_AS5, 16, NOTE_D5, 16,
  NOTE_A5, 16, NOTE_D5, 16, NOTE_F5, 16, NOTE_D5, 16, NOTE_A5, 16, NOTE_D5, 16, NOTE_G5, 16, NOTE_D5, 16,
  NOTE_AS5, 16, NOTE_D5, 16, NOTE_D6, 16, NOTE_D5, 16, NOTE_C6, 16, NOTE_D5, 16, NOTE_AS5, 16, NOTE_D5, 16,

  NOTE_A5, 16, NOTE_D5, 16, NOTE_AS5, 16, NOTE_D5, 16, NOTE_A5, 16, NOTE_D5, 16, NOTE_G5, 16, NOTE_D5, 16,
  NOTE_A5, 16, NOTE_D5, 16, NOTE_AS5, 16, NOTE_D5, 16, NOTE_C6, 16, NOTE_D5, 16, NOTE_AS5, 16, NOTE_D5, 16,
  NOTE_A5, 16, NOTE_D5, 16, NOTE_F5, 16, NOTE_D5, 16, NOTE_A5, 16, NOTE_D5, 16, NOTE_G5, 16, NOTE_D5, 16,
  NOTE_C6, 16, NOTE_C6, 16, NOTE_F6, 16, NOTE_D6, 8, REST, 16, REST, 8,
  REST, 4, NOTE_C6, 16, NOTE_AS5, 16,

  NOTE_C6, -8,  NOTE_F6, -8, NOTE_D6, -4, //35
  NOTE_C6, 8, NOTE_AS5, 8,
  NOTE_C6, 8, NOTE_F6, 16, NOTE_D6, 8, REST, 16, REST, 8,
  REST, 4, NOTE_C6, 8, NOTE_D6, 8,
  NOTE_DS6, -8, NOTE_F6, -8,

  NOTE_D6, -8, REST, 16, NOTE_DS6, 8, REST, 8, //40
  NOTE_C6, 8, NOTE_F6, 16, NOTE_D6, 8, REST, 16, REST, 8,
  REST, 4, NOTE_C6, 8, NOTE_AS5, 8,
  NOTE_C6, -8,  NOTE_F6, -8, NOTE_D6, -4,
  NOTE_C6, 8, NOTE_AS5, 8,

  NOTE_C6, 8, NOTE_F6, 16, NOTE_D6, 8, REST, 16, REST, 8, //45
  REST, 4, NOTE_C6, 8, NOTE_D6, 8,
  NOTE_DS6, -8, NOTE_F6, -8,
  NOTE_D5, 8, NOTE_FS5, 8, NOTE_F5, 8, NOTE_A5, 8,
  NOTE_A5, -8, NOTE_G5, -4,

  NOTE_A5, -8, NOTE_G5, -4, //50
  NOTE_A5, -8, NOTE_G5, -4,
  NOTE_AS5, 8, NOTE_A5, 8, NOTE_G5, 8, NOTE_F5, 8,
  NOTE_A5, -8, NOTE_G5, -8, NOTE_D5, 8,
  NOTE_A5, -8, NOTE_G5, -8, NOTE_D5, 8,
  NOTE_A5, -8, NOTE_G5, -8, NOTE_D5, 8,

  NOTE_AS5, 4, NOTE_C6, 4, NOTE_A5, 4, NOTE_AS5, 4,
  NOTE_G5,16, NOTE_D5,16, NOTE_D6,16, NOTE_D5,16, NOTE_C6,16, NOTE_D5,16, NOTE_AS5,16, NOTE_D5,16,//56 //r
  NOTE_A5,16, NOTE_D5,16, NOTE_AS5,16, NOTE_D5,16, NOTE_A5,16, NOTE_D5,16, NOTE_G5,16, NOTE_D5,16,
  NOTE_A5,16, NOTE_D5,16, NOTE_AS5,16, NOTE_D5,16, NOTE_C6,16, NOTE_D5,16, NOTE_AS5,16, NOTE_D5,16,
  NOTE_A5,16, NOTE_D5,16, NOTE_F5,16, NOTE_D5,16, NOTE_A5,16, NOTE_D5,16, NOTE_G5,16, NOTE_D5,16,

  NOTE_G5,16, NOTE_D5,16, NOTE_D6,16, NOTE_D5,16, NOTE_C6,16, NOTE_D5,16, NOTE_AS5,16, NOTE_D5,16,//61
  NOTE_A5,16, NOTE_D5,16, NOTE_AS5,16, NOTE_D5,16, NOTE_A5,16, NOTE_D5,16, NOTE_AS5,16, NOTE_D5,16,
  NOTE_A5,16, NOTE_D5,16, NOTE_AS5,16, NOTE_D5,16, NOTE_C6,16, NOTE_D5,16, NOTE_AS5,16, NOTE_D5,16,
  NOTE_A5,16, NOTE_D5,16, NOTE_F5,16, NOTE_D5,16, NOTE_A5,16, NOTE_D5,16, NOTE_G5,16, NOTE_D5,16,
  NOTE_G5,16, NOTE_D5,16, NOTE_D6,16, NOTE_D5,16, NOTE_C6,16, NOTE_D5,16, NOTE_AS5,16, NOTE_D5,16,
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

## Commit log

2021-09-22 Create README.md
    adding a Readme to explain the role of the PCB in MiniCat 2.0
2021-09-22 Add files via upload
    adding the Fritzing PCB file created directly as PCB (no schematics)
    [MiniCat_2.0_PCB_1_0.fzz]
2021-10-08 Create minicat_buzzer_test.ino
    roboticsformakers.com
    0. plug the arduino nano board and the buzzer on the green PCB and upload this code into Arduino to test the buzzer
    [minicat_buzzer_test.ino]
2021-10-15 Add files via upload
    Bill Of Material MiniCat
    [BoM_Electronics_Minicat.xlsx]
2021-10-22 Create CAD
2021-10-22 Add files via upload
    .stp file for the MiniCat Robot Full Assembly
    [MiniCat_full_assembly.stp]
2021-10-31 Add files via upload
    v32
    [MiniCat_full_assembly.step]
2021-10-31 Add files via upload
    export from Fusion360 to standard CAD .stp or .step files was losing infos about the Sketch created, so we decided to keep the original Fusion360 .f3d format
    [MiniCat_full_assembly v32.f3d]
2021-11-01 Create README.md
    adding IRremote test Software based on IRremote library (need to ne installed in your Arduino IDE : Tools/Manage Libraries “IRremote”)
2021-11-01 Add files via upload
    adding IRremote_test.ino, based on IRremote lib (Manage Libraries in Arduino IDE)
2021-11-01 Create README.md
    Adding minicat_i2c_test.ino to test the I2C communication and Master (Arduino) - Slaves (Servo driver board and Gyroscope) present.
2021-11-01 Create README.md
    Adding minicat_one_servo_test.ino to test the servo driver board and 1x Servomotor
2021-11-01 Add files via upload
    minicat_one_servo_test.ino, allow you to test all 8 servos one by one by changing their angles
2021-11-02 Create README.md
    adding minicat_gyro_test for testing the MPU6050 Gyroscope feature
2021-11-03 Create README.md
    Adding minicat_servos_and_gyro_calibration.ino in order to :
    - put all servos at their central zero position before mounting the legs of MiniCat
    - meassure the offset of the gyro yaw pitch roll angles compared to the default zero angles in the Gyro board firmware (MiniCat should be put on a flat surface)
2021-11-03 Add files via upload
    - measure the offset of the gyro yaw pitch roll angles compared to the default zero angles in the Gyro board firmware (MiniCat should be put on a flat surface)
    Remark : the gyro angles offset values will be stored in the EEPROM (non volatile memory of Arduino Nano) so that this Calibration is needed only once for one particular Arduino Board
    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
2021-11-05 Create README.md
    .gcode generated from “minicat-main\minicat-main\3D_printing\STL\3__all_miniToe_rubber.stl” file
    and with the TPU profile from https://github.com/alex8411/minicat/tree/main/3D_printing/printing_profiles/ender3pro/tpu
2021-11-23 Add files via upload
    fixing the missing INT (MPU6050) to D2 (Arduino) connection
    [MiniCat_Buzzer_Infrared_Servo_IMU_EYES__FULL__Sketch.fzz, MiniCat_Buzzer_Infrared_Servo_IMU__FULL__Sketch.fzz]
2021-12-23 Add files via upload
    adding the 1 layer optimized PCB for CNC milling
    [MiniCat_2.0_PCB_1x_LAYER_1_0.fzz]
2022-01-02 Create README.md
    adding details on the Nano V3.0 Clone usb to serial chip driver
2022-01-02 Add files via upload
    driver from http://www.wch.cn/download/CH341SER_EXE.html
